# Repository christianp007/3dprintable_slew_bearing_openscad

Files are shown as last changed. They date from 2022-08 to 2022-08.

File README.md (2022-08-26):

# 3dprintable_slew_bearing_openscad
A 3d printable customizable slew bearing designed with OpenSCAD

This is a complete reimplementation in OpenSCAD of the slew bearing created by Christoph Laimer. He implemented it in Fusion360 and made a nice Youtube video on how to design such a thing and testing it, highly recommended!

The main features of this over the one by Christoph Laimer are:
- customizable in Customizer
- integrated threads, so no need for additional screws
- tension adjustable (unscrew a bit to reduce tension)

I highly recommend printing the rollers in vase mode to get best possible surface quality. If your slicer allows, add some bottom and top layers to make the rollers stiffer.
The outer ring can be printed in one part, but two parts may provide better surface quality because otherwise there is a 45 degrees overhang.

The bearing height will determine your roller diameter and height, i recommend using a height of 8mm or more, otherwise it might be challanging to print and tolerances must be small.
I successfully printed bearings from 70x25mm diameter down to 13x2.5mm.
Without screwable outer ring 11mm should be possible. Rollers cant be printed that small, but you can use small chunks of 1.75mm filament as rollers.

Hints:
- Number of rollers are not (yet) automatically optimized. You should design it with minimal distance between rollers and number of rollers must be even! Easiest to adjust by changing height of bearing
- This does not feature the very cool kegel style rollers as designed by Christopf Laimer

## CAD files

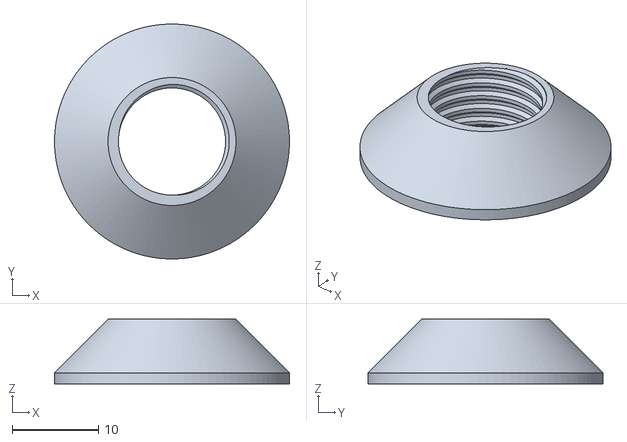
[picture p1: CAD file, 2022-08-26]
slew_bearing_49x15x8_INNER_TOP.stl
27.3 x 27.3 x 7.50

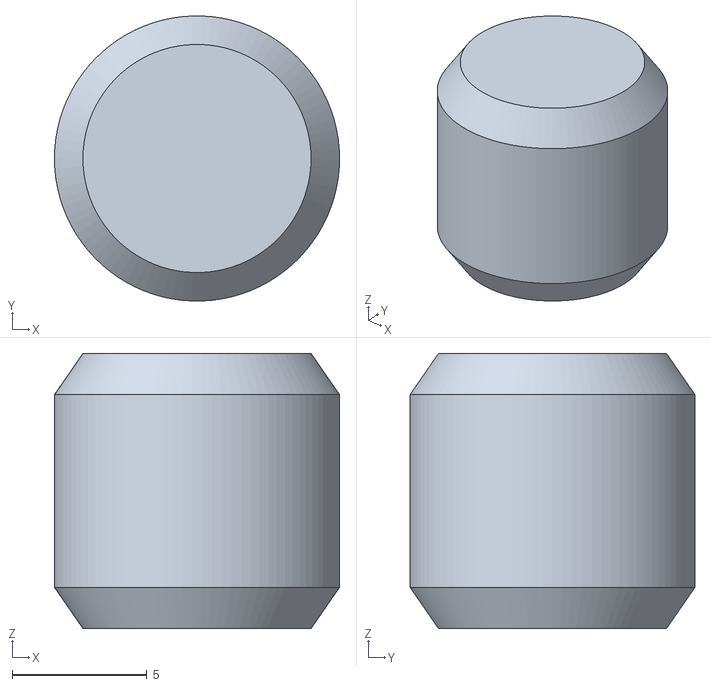
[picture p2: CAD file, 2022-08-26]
slew_bearing_49x15x8_ROLLER.stl
10.6 x 10.6 x 10.2

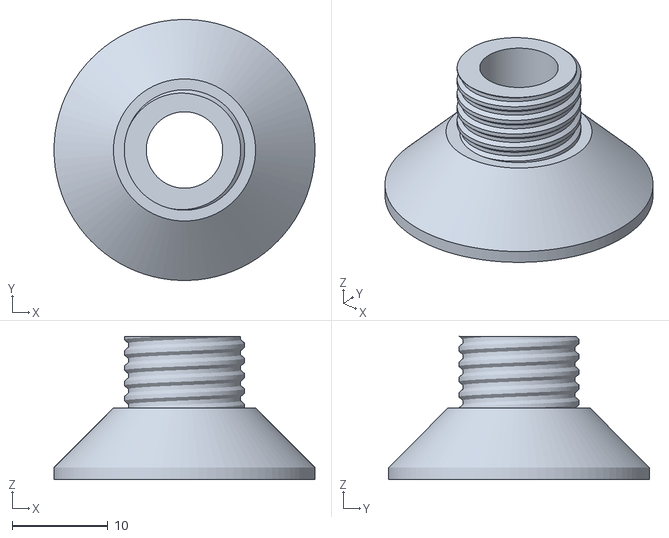
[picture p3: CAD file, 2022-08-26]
slew_bearing_49x15x8_INNER_BOTTOM.stl
27.3 x 27.3 x 15.0

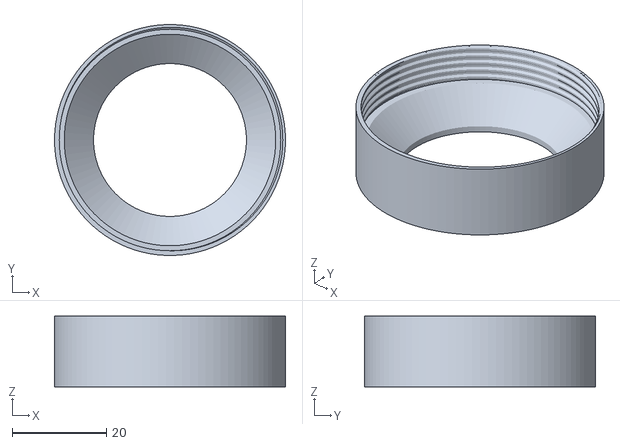
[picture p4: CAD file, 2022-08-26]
slew_bearing_49x15x8_OUTER_TOP.stl
49.0 x 49.0 x 15.0

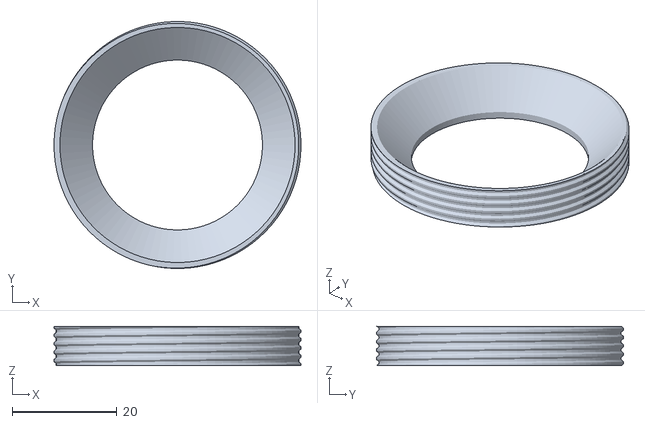
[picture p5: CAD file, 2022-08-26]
slew_bearing_49x15x8_OUTER_BOTTOM.stl
47.1 x 47.1 x 7.50

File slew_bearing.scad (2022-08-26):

/* [Main] */
// which parts to render - use one at a time to generate printable stl files (sadly OpenSCAD cannot generate multiple stl files at once)
SHOW_PART="ALL"; // [ALL,INNER_BOTTOM,INNER_TOP,OUTER_BOTTOM,OUTER_TOP,OUTER_BOTH,ROLLER]
// larger values increase calculation time considerably, choose small values for rapid prototyping
quality=90; // [30:20:150]
// print width, as configured in your slicer (use nozzle width if not configurable)
nozzle=0.42;
// outer diameter of bearing
outerDiameter=49;
// inner diameter of bearing, may be 0
innerDiameter=8;
// height of bearing, will indirectly define roller diameter and heigth
height=15;

// space between outer and inner, not very critical, will be limited to half roller height; 0=automatic
config_opening_between_inner_outer=0; // [0:0.5:10]

/* [Tolerances] */
// main tolerance setting
tolerance=0.2;
// tolerance for roller diameter, critical to optimize this for quality of bearing
toleranceRollerDiameter=0.03;
// tolerance of the threading
threadTolerance=0.35;

/* [Roller] */
// chamfer factor in percent of roller height, 100=completely chamfer top and bottom half
rollerChamferFactorPercent=30; // [10:5:100]
// how much chamfer is applied, in percent of diameter, 100=chamfer down to 0
rollerChamferAmountFactorPercent=20; 
// the roller position, larger values can fit more rollers, extreme values limit thickness of outer/inner walls to a minimum; 0=as close as possible to inner bearing diameter, 100=as close as possible to outer bearing diameter
rollerPositionPercent=80; // [0:5:100]

/* [Threads ]*/
// thread thickness, must be at least nozzle width; 0=automatic
config_threadThickness=0; // [0:0.1:5]
// if the outer ring should have threads, if false you have to print the outer ring as one piece or glue it togehter. Saves space for threads so outer bearing diameter can be smaller.
createThreadsForOuterRing=true; // [true,false]
// position of inner thread; 0=as close as possible to inner hole, 100=as close as possible to rollers
posInnerThread=80; // [0:10:100]
// position of outer thread; 0=as close as possible to rollers, 100=as close as possible to outer bearing diameter
posOuterThread=80; // [0:10:100]

/* [Hidden] */
$fn=quality;

rollerChamferFactor=rollerChamferFactorPercent/100/2;
chamferAmountFactor=rollerChamferAmountFactorPercent/100;

threadThickness=max(config_threadThickness,nozzle);

c=sqrt(2*height/2*height/2); // pythagoras triangle

rollerHeight=c-2*tolerance;

threadWallThickness=2*nozzle+2*threadThickness;
singleThreadSpace=4*nozzle+2*threadThickness+2*threadTolerance;
numThreads=createThreadsForOuterRing ? 2 : 1;
totalThreadSpace=numThreads*singleThreadSpace+(createThreadsForOuterRing?0:2*nozzle);

tmp_opening_between_inner_outer=config_opening_between_inner_outer==0 ? rollerHeight/4 : min(config_opening_between_inner_outer,rollerHeight/2);
opening_between_inner_outer=max(tmp_opening_between_inner_outer,2*tolerance);

// available horizontal space to wiggle with
horizontalRollerSpace=sqrt(2*c*c); // pythagoras triangle, will currently always result in value of variable 'height'
availableHorizontalWiggleSpace=outerDiameter-2*horizontalRollerSpace-totalThreadSpace-innerDiameter;
echo("availableHorizontalWiggleSpace",availableHorizontalWiggleSpace);
innerExtraWallWiggleRoom=availableHorizontalWiggleSpace*(rollerPositionPercent/100);
innerExtraWall=singleThreadSpace/2+innerExtraWallWiggleRoom/2;
outerExtraWallWiggleRoom=availableHorizontalWiggleSpace*(1-(rollerPositionPercent/100));
outerExtraWall=(outerDiameter-innerDiameter)/2-innerExtraWall-horizontalRollerSpace;
echo("outerExtraWall",outerExtraWall);

// --- BEGIN roller calculation ---
middleRollerCircleDiameter=innerDiameter+2*innerExtraWall+height;
middleRollerCircleCircumference = 3.141592*middleRollerCircleDiameter;

middleRollerDiameter=c-toleranceRollerDiameter;
innerRollerDiameter=middleRollerDiameter;
outerRollerDiameter=middleRollerDiameter;
rollerDiameterDifference=outerRollerDiameter-innerRollerDiameter;

spaceAtInnerWallForRollers=3.141592*(middleRollerCircleDiameter-(c/4));
spaceForNumRollers=spaceAtInnerWallForRollers/middleRollerDiameter;
// --- END roller calculation ---

innerThreadDiameter=innerDiameter+threadWallThickness+(innerExtraWallWiggleRoom*(posInnerThread/100));
outerThreadDiameter=outerDiameter-threadWallThickness-(outerExtraWallWiggleRoom*(1-(posOuterThread/100)));

OVERLAP=0.001;

echo("rollerHeight", rollerHeight);
echo("middleRollerDiameter",middleRollerDiameter);
echo("spaceForNumRollers",spaceForNumRollers);


// top parts must be rotated so large side is on bottom
rotate_top_to_make_printable=(len(search("_TOP",SHOW_PART))>=4) ? 180 : 0;

color([0.5,0.5,0.5])
rotate([rotate_top_to_make_printable,0,0])
{
    if (showpart("OUTER_BOTTOM") || SHOW_PART=="OUTER_BOTH"){
        outer0();
    }
    if (showpart("OUTER_TOP") || SHOW_PART=="OUTER_BOTH"){
        outer1();
    }
    if (showpart("INNER_BOTTOM")){
        inner0();
    }
    if (showpart("INNER_TOP")){
        inner1();
    }
}
color([0.3,0.4,1])
{
    if (showpart("ROLLER")){
        if (SHOW_PART=="ALL"){
            renderRollerInBearing();
        } else {
            roller();
        }
    }
}


function showpart(partId) = SHOW_PART=="ALL" ||  SHOW_PART==partId;

module renderRollerInBearing(){
    numRollers=floor(spaceForNumRollers);
    
    for (i=[0:numRollers-1]){
        rotationDirection=(i%2==0) ? 1 : -1;
        
        degrees_per_roller=360/numRollers;
        maxPosFromCenter=middleRollerCircleDiameter/2;
        translate([cos(i*degrees_per_roller)*maxPosFromCenter,sin(i*degrees_per_roller)*maxPosFromCenter,height/2])
        rotate([rotationDirection*-sin(i*degrees_per_roller)*45,rotationDirection*cos(i*degrees_per_roller)*45,0])
        translate([0,0,-rollerHeight/2])
        roller();
    }
    
}

module outer0(){
    difference(){
        half(false,outerExtraWall);
        
        if (createThreadsForOuterRing){
            translate([0,0,-OVERLAP/2])
            difference(){        
                cylinder(d=outerDiameter+1,h=height/2+OVERLAP);
                translate([0,0,-OVERLAP/2])
                cylinder(d=outerThreadDiameter-2*threadThickness-0.3,h=height/2+2*OVERLAP);
            }
        }
    }
    
    if (createThreadsForOuterRing){
        translate([0,0,+OVERLAP/2])
        thread(height/2-OVERLAP,outerThreadDiameter,threadThickness,1.6,true,false);
    }
}

module outer1(){
    difference(){
        translate([0,0,height])
        rotate([180,0,0])
        half(false,outerExtraWall);
    }
    
    if (createThreadsForOuterRing){
        union(){
            translate([0,0,+OVERLAP/2])
            thread(height/2-OVERLAP,outerThreadDiameter+2*threadTolerance,threadThickness,1.6,false);
            
            translate([0,0,-OVERLAP/2])
            difference(){
                cylinder(d=outerDiameter,h=height/2+OVERLAP);
                translate([0,0,-OVERLAP/2])
                cylinder(d=outerThreadDiameter+2*threadThickness+0.3,h=height/2+2*OVERLAP);
            }
        }
    }
}

module inner0(){
    difference(){
        union(){
            hull(){
                half(true,innerExtraWall);
            }
            translate([0,0,height/2-OVERLAP])
            thread(height/2,innerThreadDiameter,threadThickness,1.6,true);
        }
        
        cylinder(d=innerDiameter+OVERLAP/2,h=2*height+1);
    }
}

module inner1(){
    difference(){
        union(){
            difference(){
                translate([0,0,height])
                rotate([180,0,0])
                hull(){
                    half(true,innerExtraWall);
                }
                
                translate([0,0,height/2-0.5])
                cylinder(d=innerThreadDiameter+2*threadThickness,h=height/2+1);
            }
            
            translate([0,0,height/2-OVERLAP/2])
            thread(height/2-OVERLAP,innerThreadDiameter+2*threadTolerance,threadThickness,1.6,false);
        }
//        cylinder(d=innerDiameter+OVERLAP/2,h=2*height+1);
    }
}

module roller(){
    chamferHeight=rollerHeight*rollerChamferFactor;
    chamferDiameterDifference=rollerChamferFactor*rollerDiameterDifference;
    chamferAmount=chamferAmountFactor*outerRollerDiameter+rollerChamferFactor*rollerDiameterDifference;

    difference(){
        cylinder(d1=outerRollerDiameter,d2=innerRollerDiameter,h=rollerHeight);
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

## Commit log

2022-08-26 initial commit (current version from thingiverse)
    [slew_bearing.scad, slew_bearing_49x15x8_INNER_BOTTOM.stl, slew_bearing_49x15x8_INNER_TOP.stl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]
2022-08-26 Fixed Warnings in OpenScad 2021.01
    - removed len(<vector>) from "library" functions
    - removed unspecified parameter 'full' from call to Threading
    [slew_bearing.scad]
